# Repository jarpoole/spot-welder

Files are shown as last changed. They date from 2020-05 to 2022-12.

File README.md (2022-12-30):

# Spot Welder

## Features

1. Precise microsecond timing resolution selected via an encoder wheel.
2. Three user-programmable timing presets which are accessible via the buttons.
3. A 1/4 inch jack for an external footpedal. See the `mechanical` folder for a simple 3D printable footpedal design.

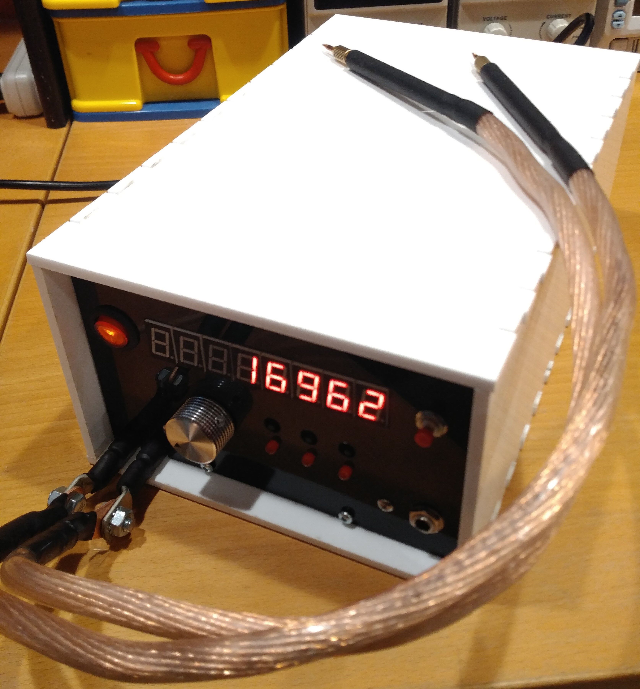
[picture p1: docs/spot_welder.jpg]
Spot Welder


## Internals

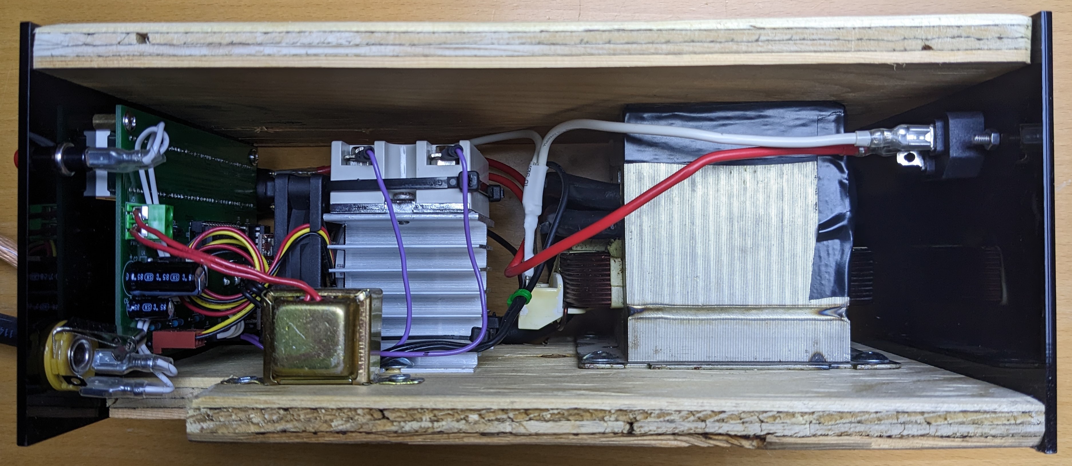
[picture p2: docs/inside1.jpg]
inside1


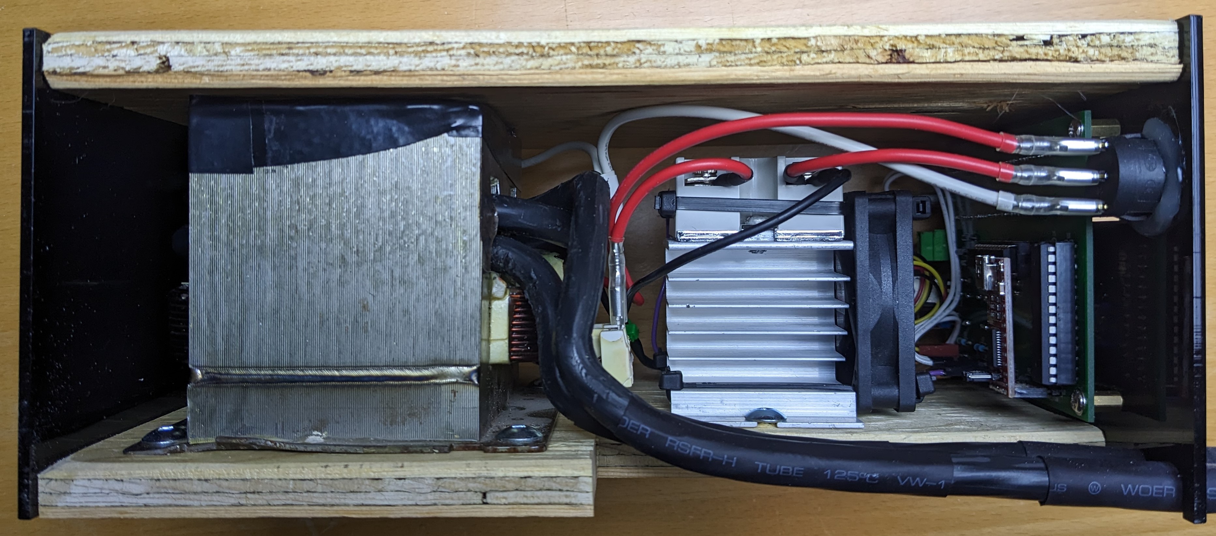
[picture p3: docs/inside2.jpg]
inside2


## Principles of Operation

The spot welder is build around a recycled microwave transformer which has had its secondary coil rewound to produce a high current and low voltage (2 turns of 4AWG). The microwave and unmodified transformer are shown below.

microwave

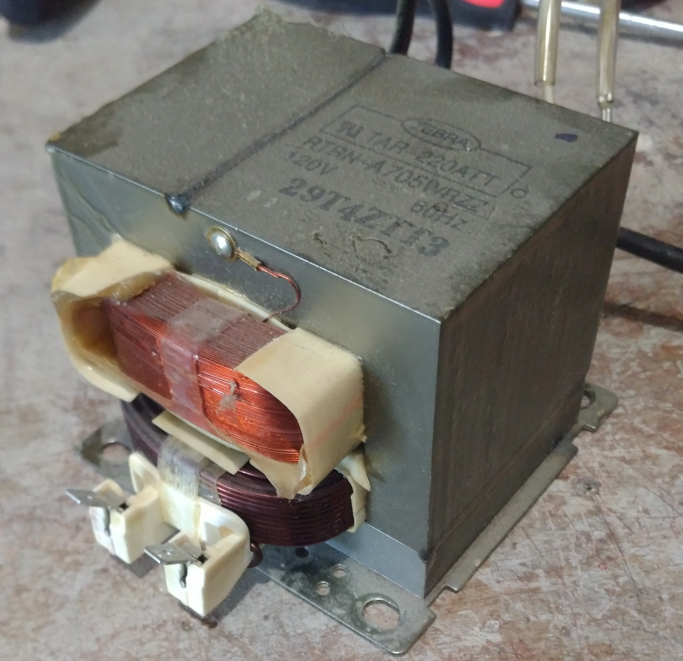
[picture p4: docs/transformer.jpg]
transformer


 A solid state relay (SSR) is used to create precise pulses to produce welds by controlling the primary side. Because of the large currents that it will need to handle it is heatsunk and actively cooled with a small computer fan.

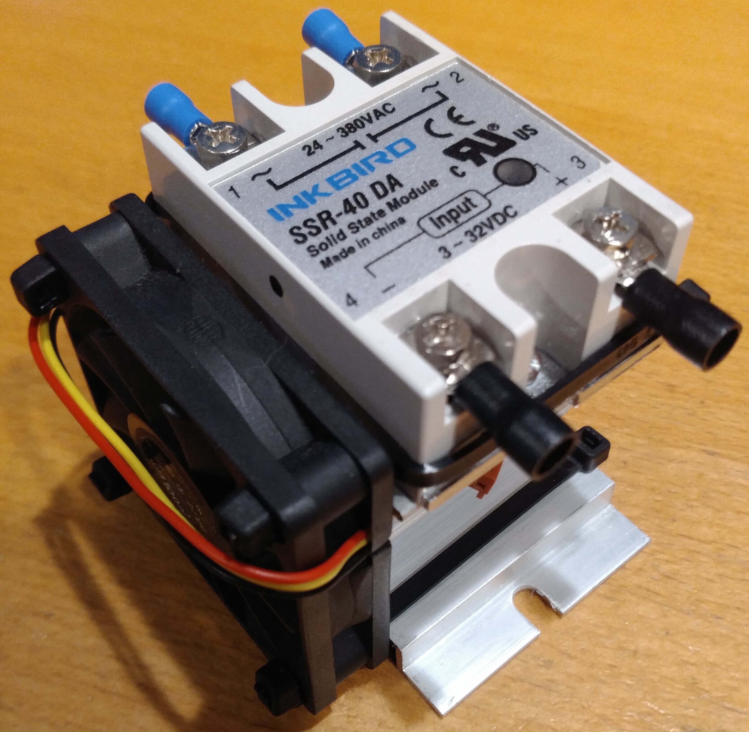
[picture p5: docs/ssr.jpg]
ssr


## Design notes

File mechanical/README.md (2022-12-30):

# Mechanical

## Footswitch

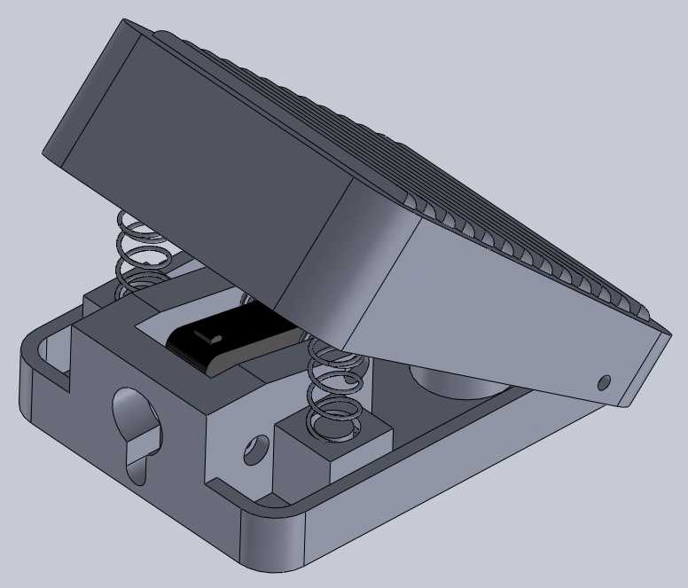
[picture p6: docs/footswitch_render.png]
footswitch


## Enclosure

The [front plate](./enclosure/front_plate.pdf) and [back plate](./enclosure/back_plate.pdf) are each around `185x130mm` and should be cut out of `3mm` acrylic.

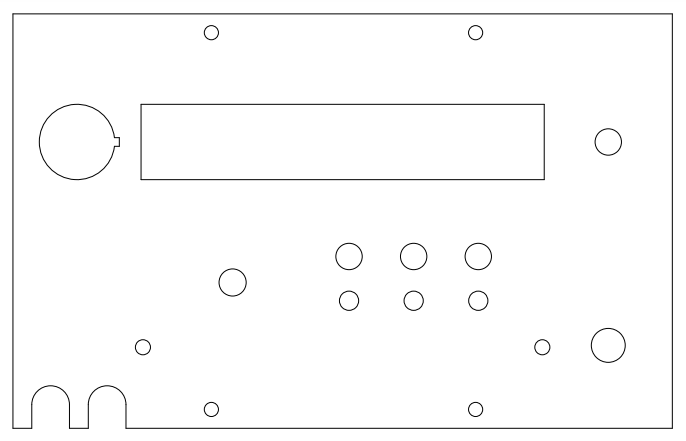
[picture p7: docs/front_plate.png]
front plate

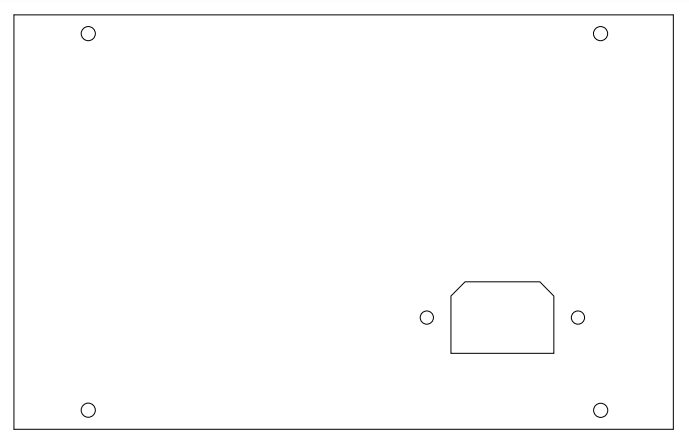
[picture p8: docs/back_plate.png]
back plate


The [shell](./enclosure/shell.pdf) requires an entire `18x24inch` sheet of 6mm acrylic.

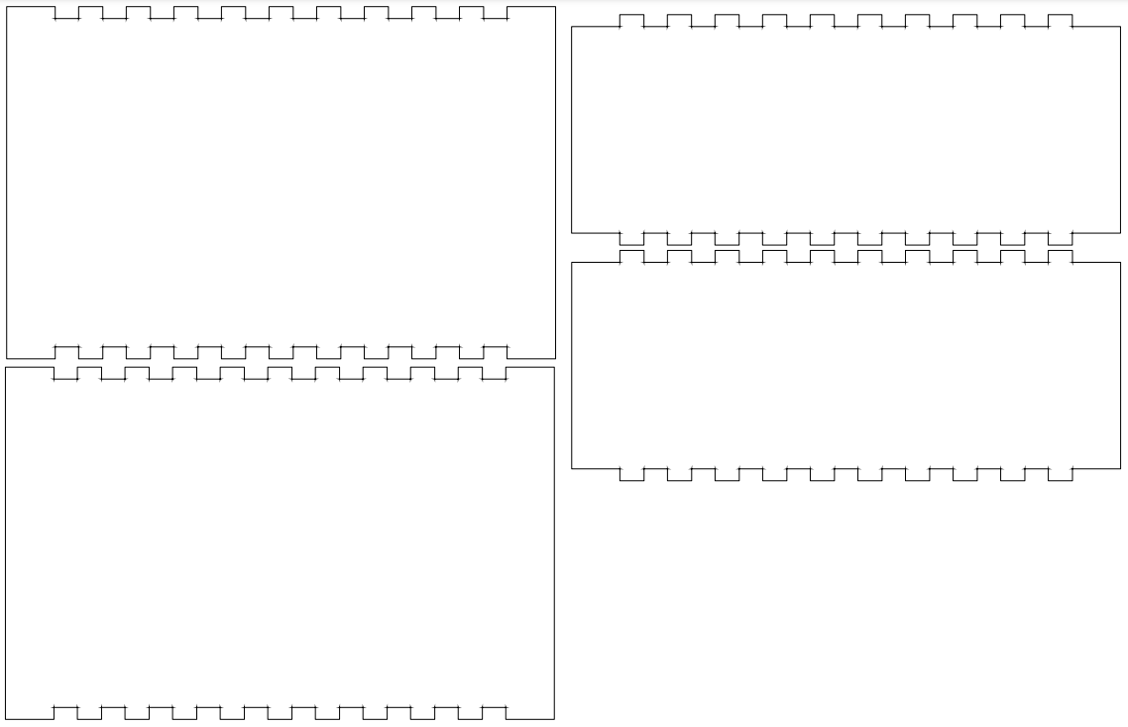
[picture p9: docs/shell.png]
shell


Finally, some small external buttons are required to extend the tactile switches on the PCB. The CAD file `button.step` is provided and can be easily 3D printed.

## Other

3 small 8mm button extenders are also needed. Their CAD model is `button.stl`.

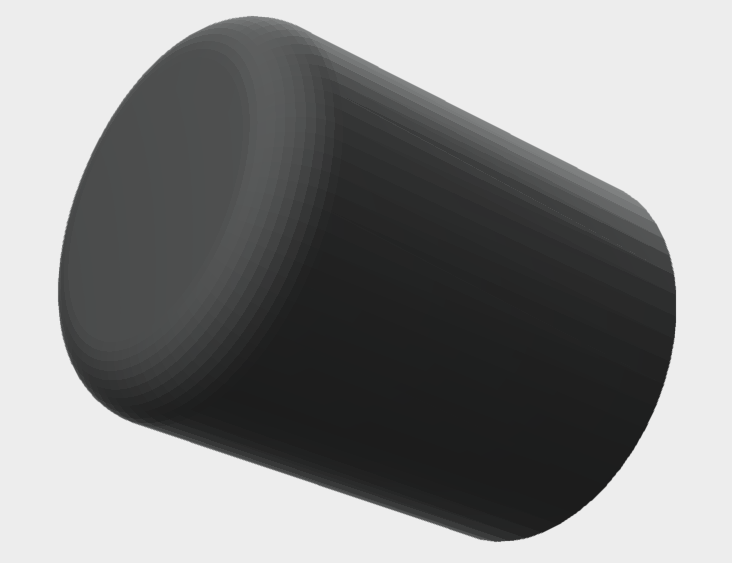
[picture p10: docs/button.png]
button


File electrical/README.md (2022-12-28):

# Electrical

## Design Software

Designed with [DipTrace](https://diptrace.com/). Sourcefiles for both the schematic (`schematic.dch`) and pcb (`pcb.dip`) are provided.

## Schematic

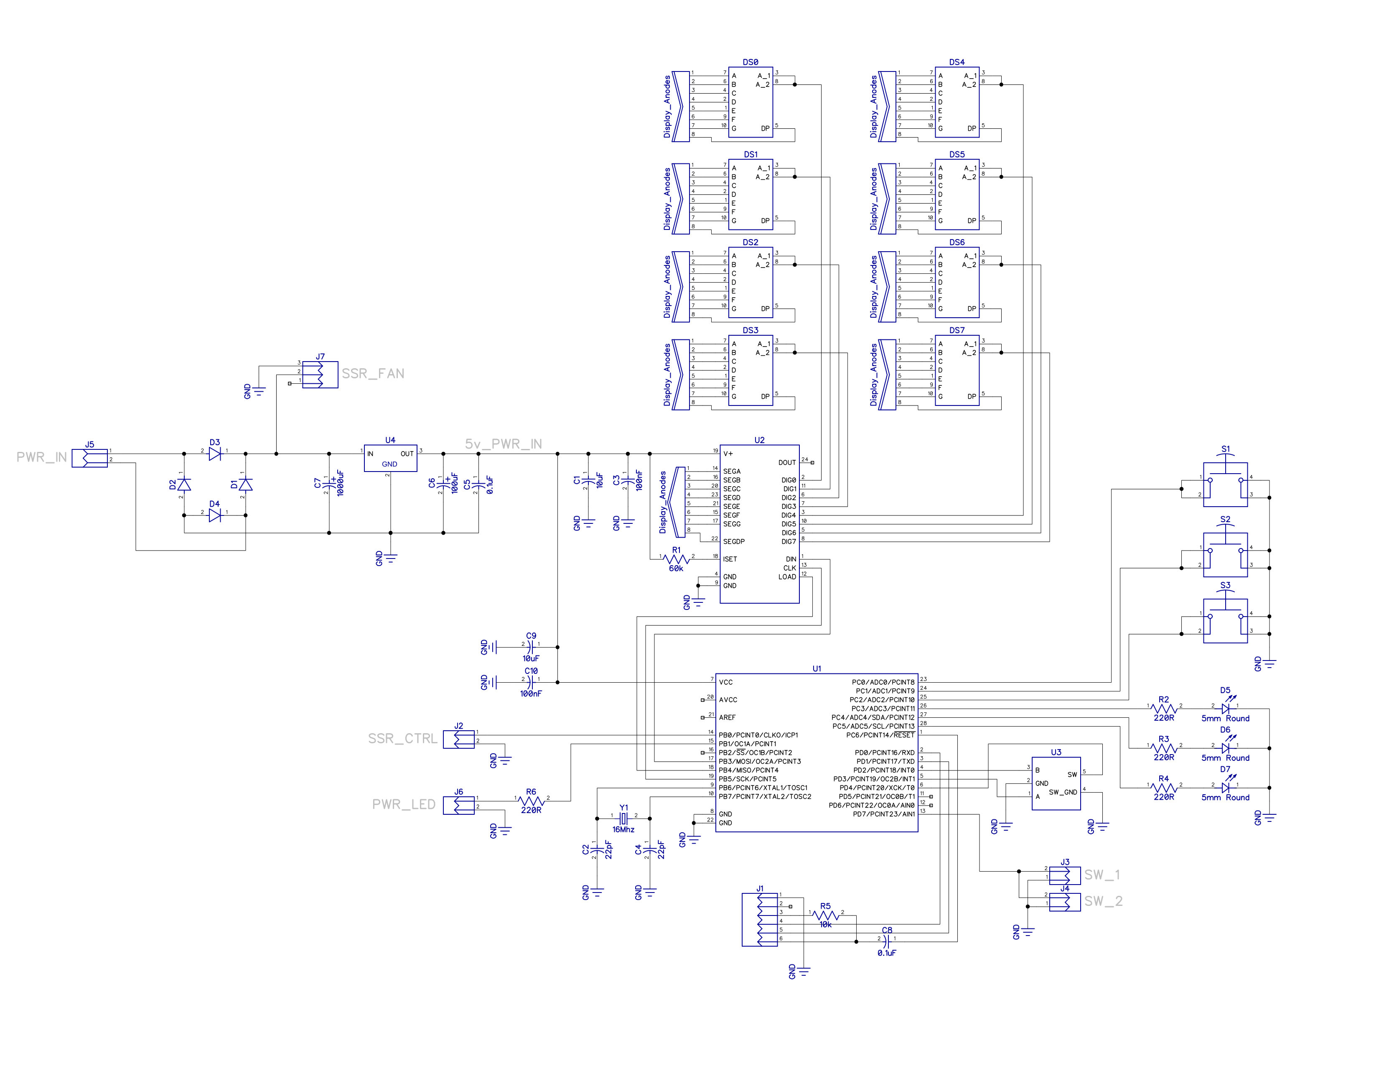
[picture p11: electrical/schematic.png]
schematic


## PCB

Most of the 3D models used for these renders are included in DipTrace's 3D model [download](https://diptrace.com/download/libraries-and-3d-models/). The models for the encoder and one of the terminal blocks are included in the `3rd_party` directory.

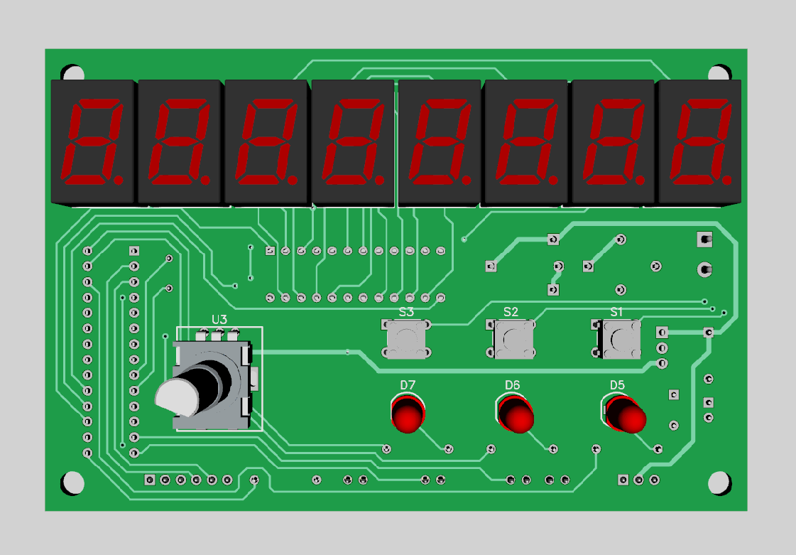
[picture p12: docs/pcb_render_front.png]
front

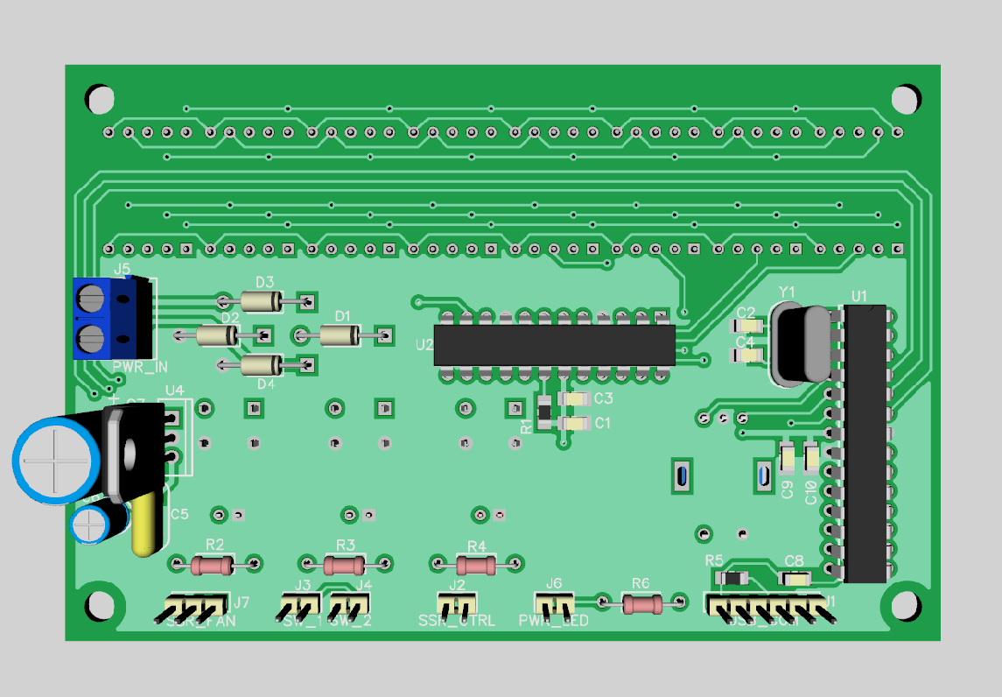
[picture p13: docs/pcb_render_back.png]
back


The generated mechanical model is also provided as `pcb.step`.

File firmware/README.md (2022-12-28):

# Firmware

## Dependencies

This project depends on the excellent `MAX7219` driver by `wayoda`. See their repository for installation instructions.

https://github.com/wayoda/LedControl
https://reference.arduino.cc/reference/en/libraries/ledcontrol/

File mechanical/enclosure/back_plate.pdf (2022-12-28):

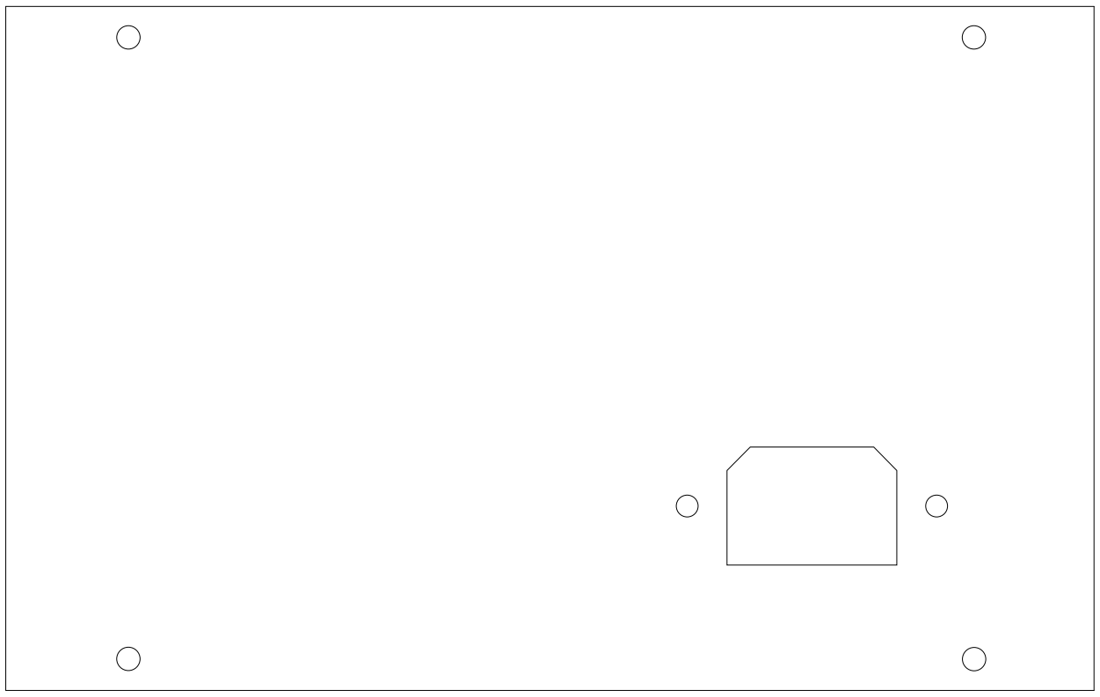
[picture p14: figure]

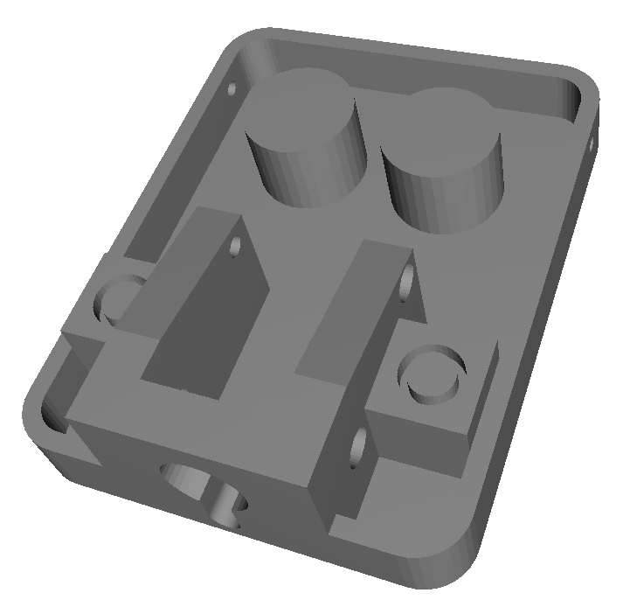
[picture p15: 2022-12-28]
docs/footswitch_base.png

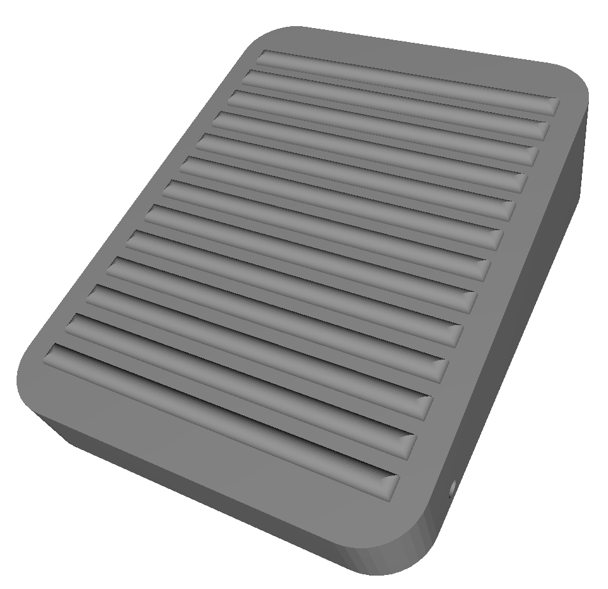
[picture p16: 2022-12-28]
docs/footswitch_top.png

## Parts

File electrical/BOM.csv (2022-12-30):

Name | Manufacturer | Quantity | RefDes | Value
CAP_1206 |  | 2 | C1, C9 | 10uF
CAP_1206 |  | 2 | C2, C4 | 22pF
CAP_1206 |  | 2 | C3, C10 | 100nF
CAP200 |  | 1 | C5 | 0.1uF
CAP100RP |  | 1 | C6 | 100uF
CAP300RP |  | 1 | C7 | 1000uF
CAP_1206 |  | 1 | C8 | 0.1uF
1N4001 |  | 4 | D1, D2, D3, D4
LED-5R_Red | Kingbright | 3 | D5, D6, D7 | 5mm Round
SA56-11EWA |  | 8 | DS0, DS1, DS2, DS3, DS4, DS5, DS6, DS7
644456-6 | TE Connectivity | 1 | J1
2 pin 2.54mm Term Block |  | 4 | J2, J3, J4, J6
OSTTA020161B | On Shore Technology | 1 | J5
644456-3 | TE Connectivity | 1 | J7
RES_1206 |  | 1 | R1 | 60k
RES400 |  | 4 | R2, R3, R4, R6 | 220R
RES_1206 |  | 1 | R5 | 10k
B3F-1000 | OMRON | 3 | S1, S2, S3
ATMEGA328_PDIP28 | Atmel | 1 | U1
MAX7219CNG | Maxim | 1 | U2
Rotary Encoder |  | 1 | U3
LM7805CT | National Semiconductor | 1 | U4
HC49S |  | 1 | Y1 | 16Mhz

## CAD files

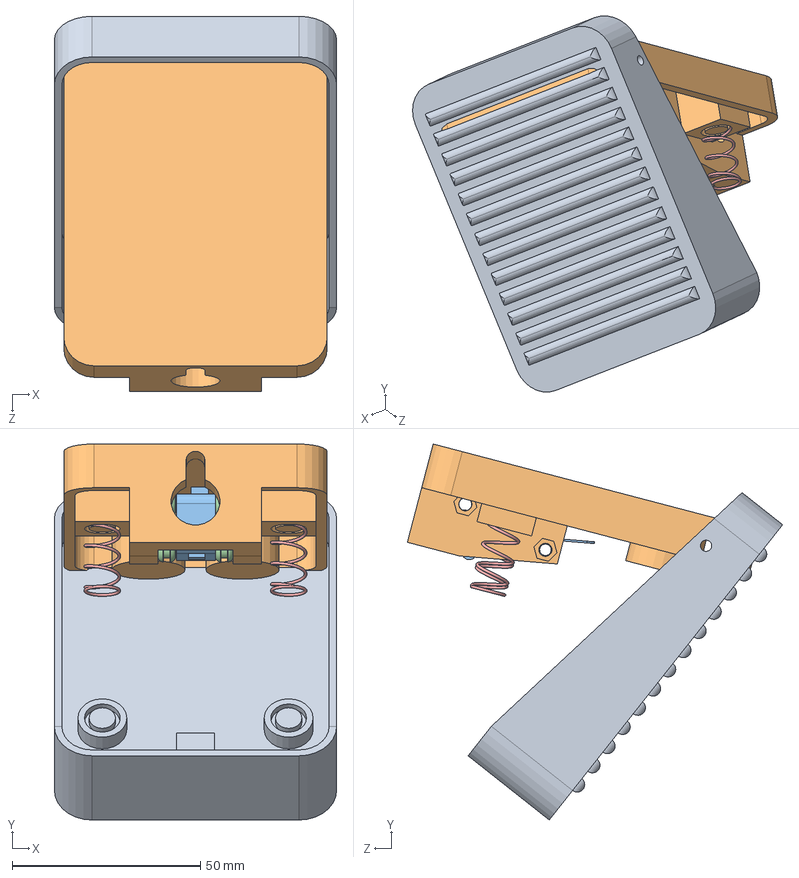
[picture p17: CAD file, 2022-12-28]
mechanical/footswitch/footswitch.SLDASM
75.0 x 99.9 x 99.7 mm
pedal
Pedal Base
V_153_1C25_BASE
Bushing x 4
Spring x 2

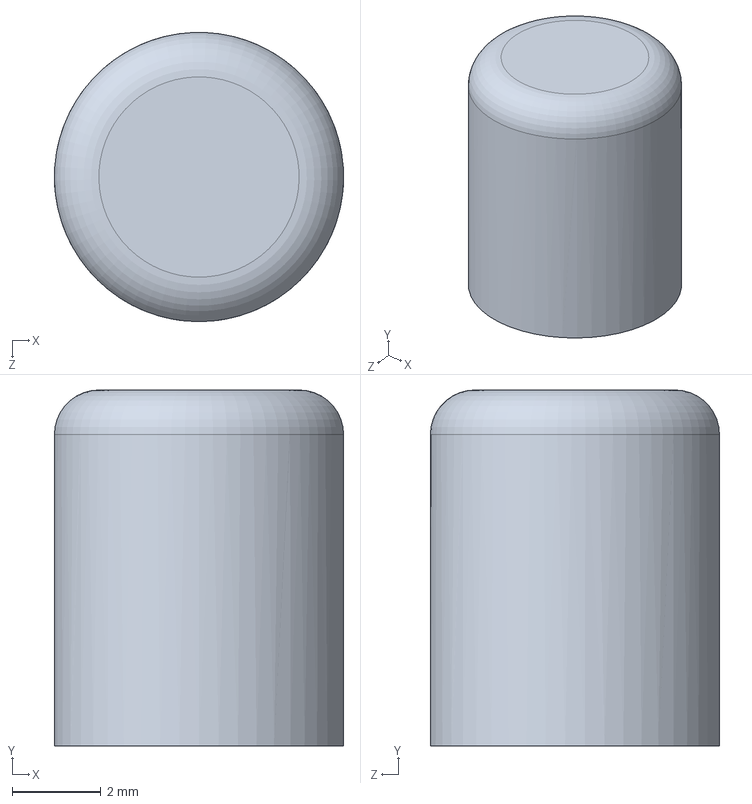
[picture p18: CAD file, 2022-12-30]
mechanical/button.SLDPRT
6.50 x 8.00 x 6.50 mm

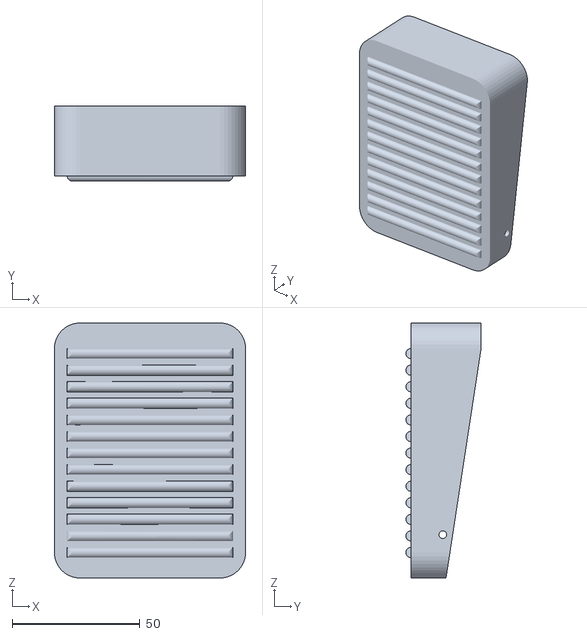
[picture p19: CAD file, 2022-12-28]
mechanical/footswitch/top.STL
75.0 x 29.5 x 100.0

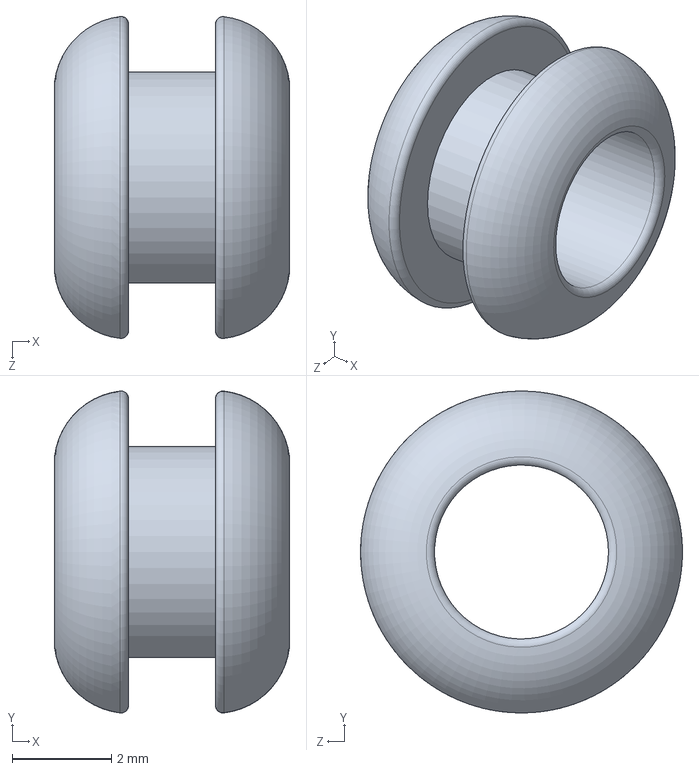
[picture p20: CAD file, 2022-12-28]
mechanical/footswitch/bushing.SLDPRT
4.73 x 6.48 x 6.48 mm

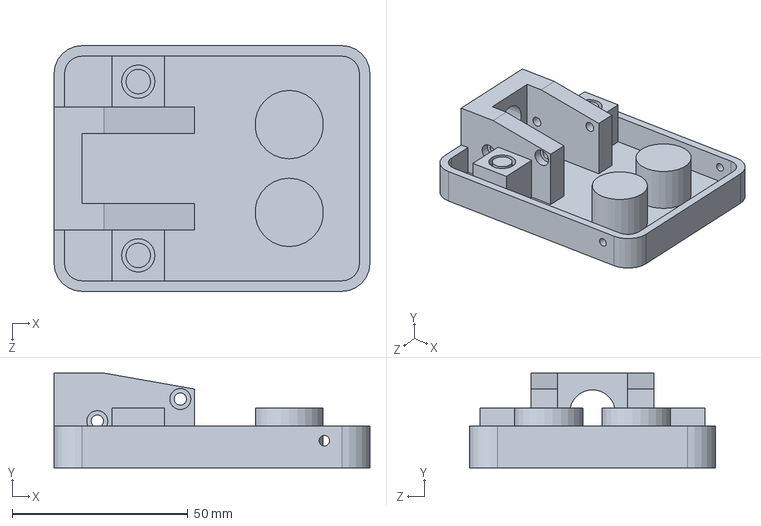
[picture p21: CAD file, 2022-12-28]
mechanical/footswitch/base.SLDPRT
90.0 x 27.0 x 70.0 mm

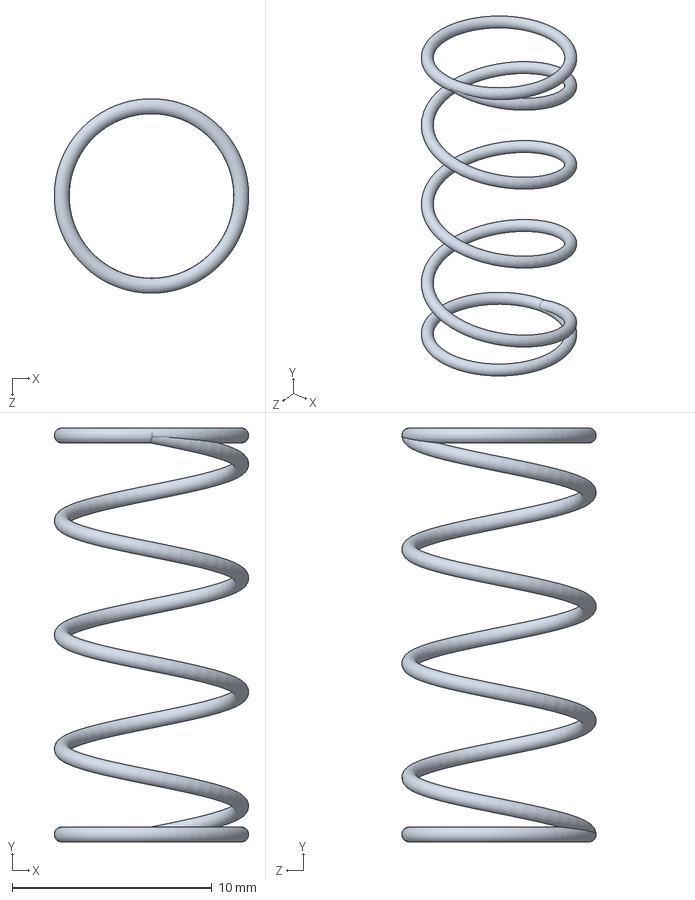
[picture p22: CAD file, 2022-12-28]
mechanical/footswitch/spring.SLDPRT
9.75 x 20.8 x 9.75 mm

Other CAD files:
mechanical/footswitch/pedal.SLDPRT
mechanical/button.STL
mechanical/footswitch/base.STL

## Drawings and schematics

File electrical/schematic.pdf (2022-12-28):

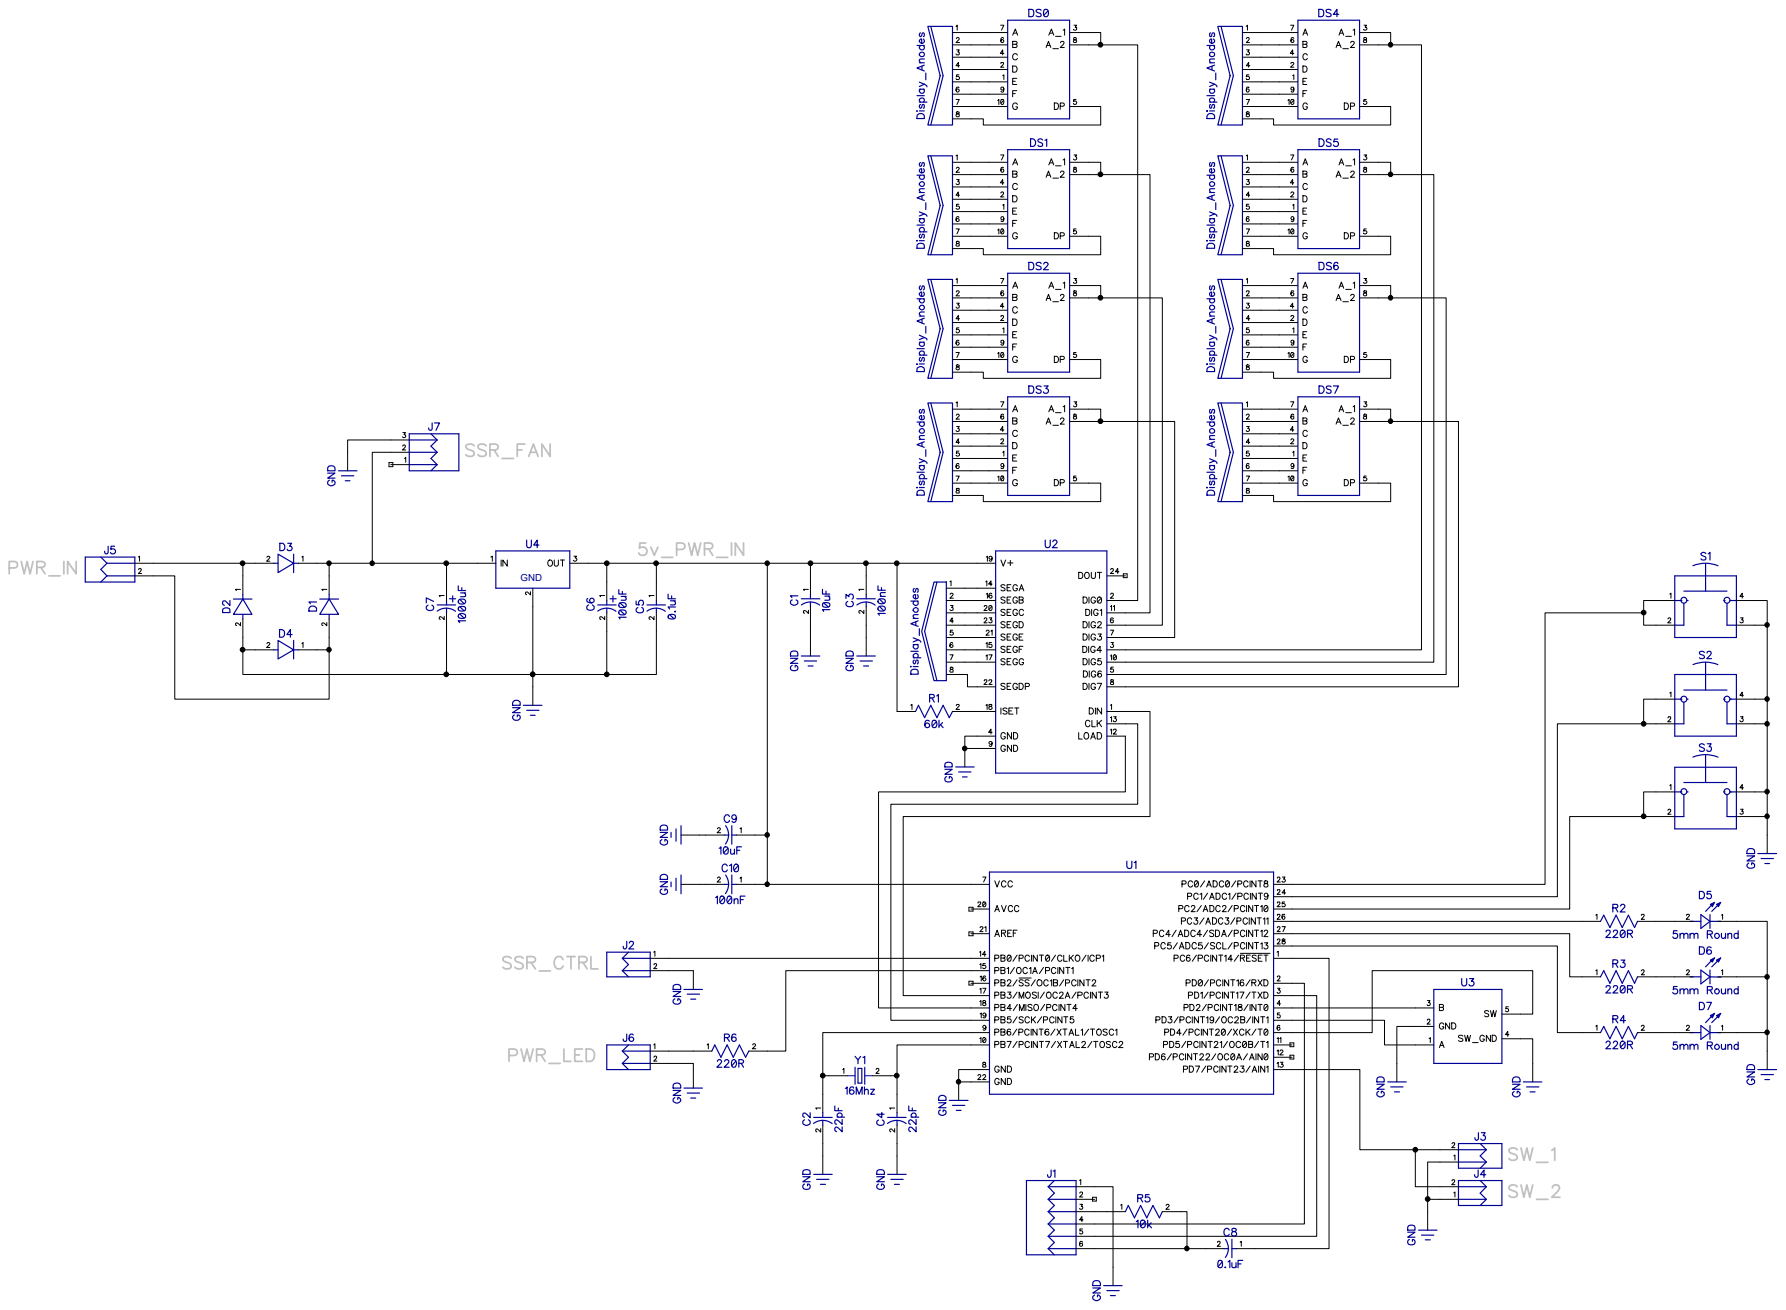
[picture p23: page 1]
GND

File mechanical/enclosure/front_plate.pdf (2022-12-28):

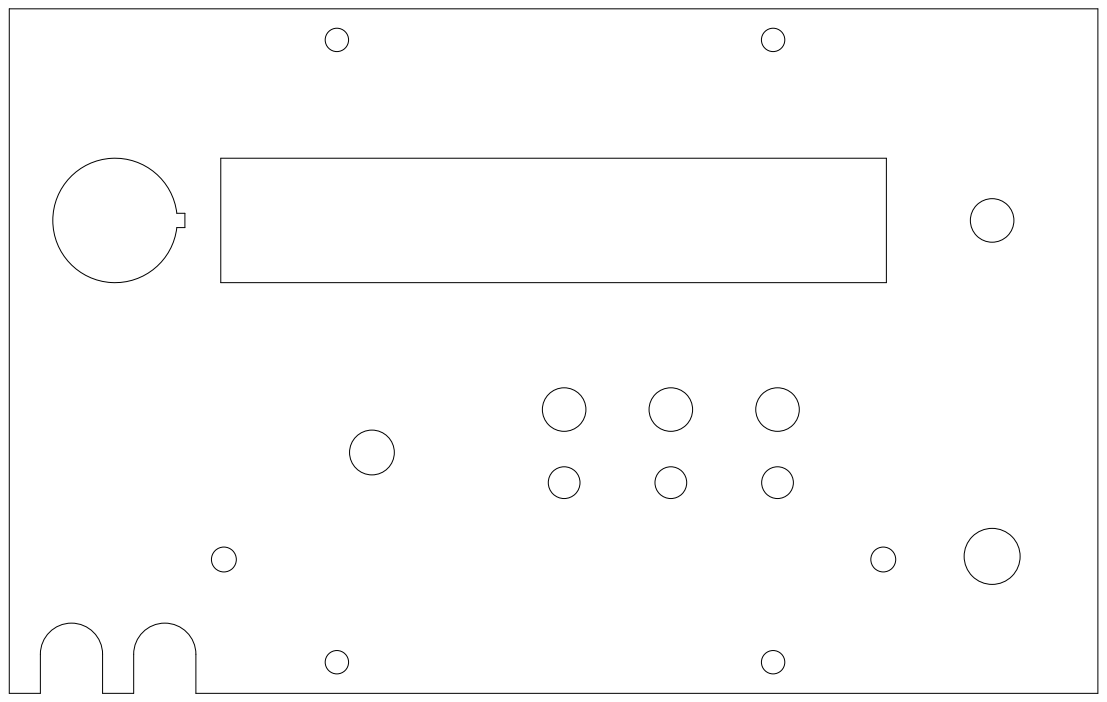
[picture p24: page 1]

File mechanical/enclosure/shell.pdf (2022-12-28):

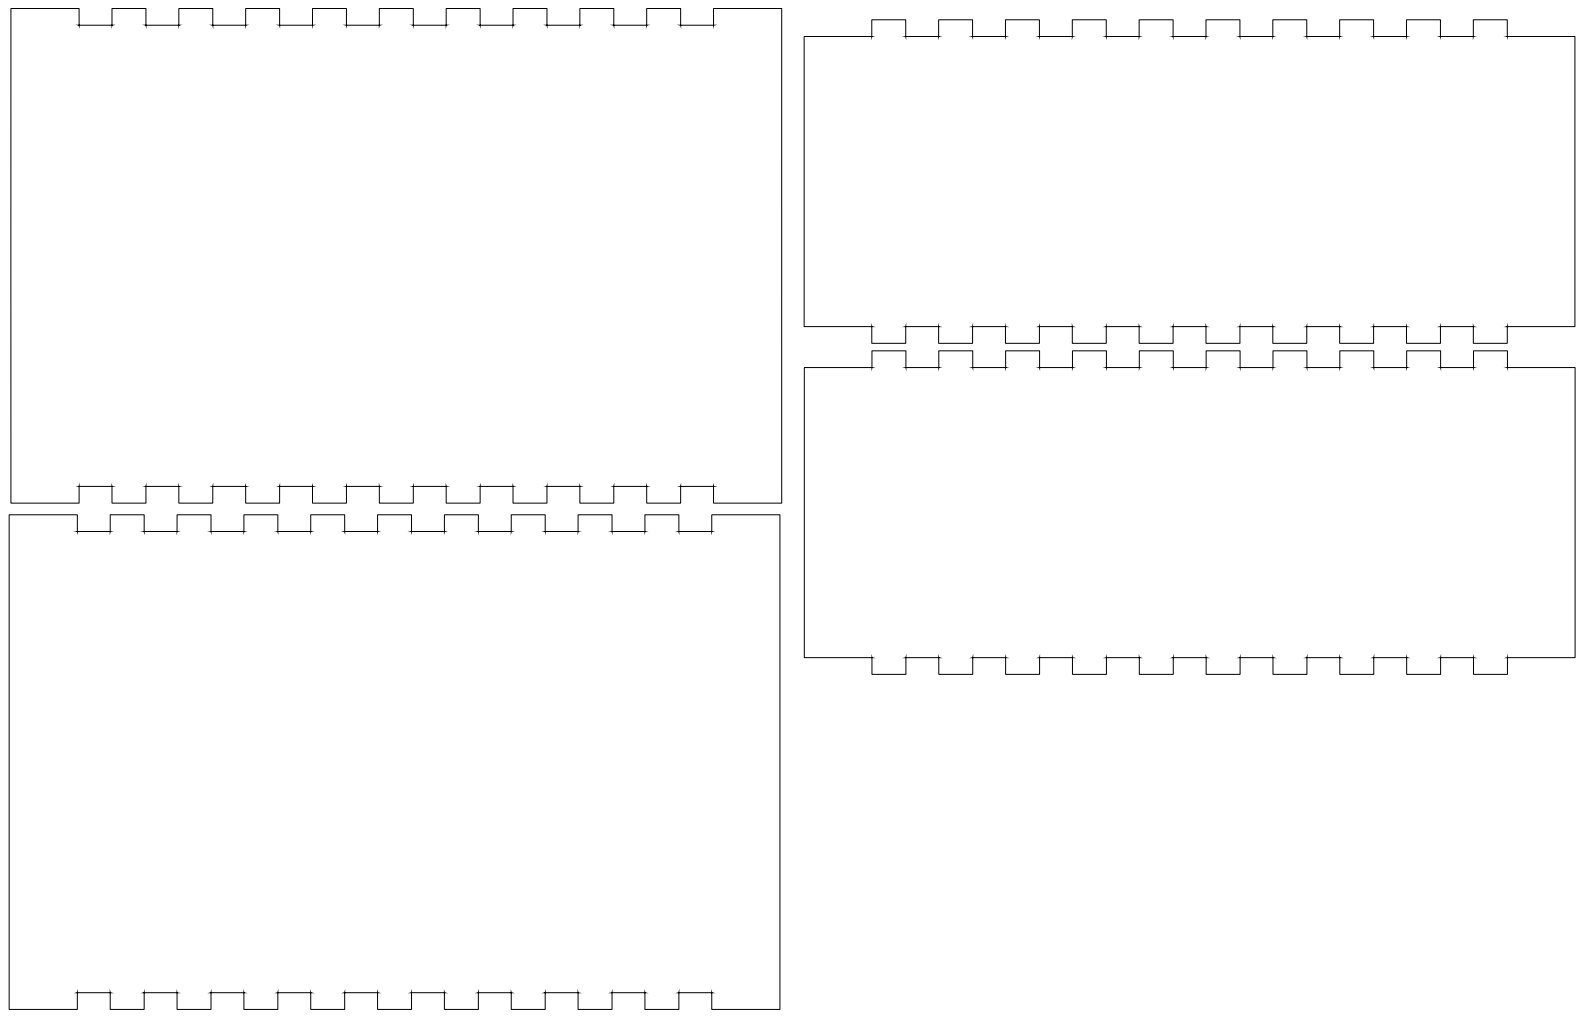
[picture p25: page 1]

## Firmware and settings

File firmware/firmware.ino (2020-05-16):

#include "LedControl.h"
#include <EEPROM.h>

// DataIn=11, CLK=13, LOAD=12, #MAX7219 devices
LedControl lc=LedControl(11,13,12,1);
//Wait a bit between updates of the display
unsigned long delaytime=250;

//Encoder Stuff
static int pinA = 2; // Our first hardware interrupt pin is digital pin 2
static int pinB = 3; // Our second hardware interrupt pin is digital pin 3
static int encoderButton = 4; // Encoder button pin
volatile byte aFlag = 0; // let's us know when we're expecting a rising edge on pinA to signal that the encoder has arrived at a detent
volatile byte bFlag = 0; // let's us know when we're expecting a rising edge on pinB to signal that the encoder has arrived at a detent (opposite direction to when aFlag is set)
volatile byte reading = 0; //somewhere to store the direct values we read from our interrupt pins before checking to see if we have moved a whole detent
volatile bool lastButtonState = false; //Last value of the encoder button
volatile long lastTickTime = 0; //Used to calculate encoder acceleration

//Control data
static int button1 = A2;
static int button2 = A1;
static int button3 = A0;
static int led1 = A5;
static int led2 = A4;
static int led3 = A3;
static long button1Time = 0;
static long button2Time = 0;
static long button3Time = 0;
static int longPressTime = 2000;
static int triggerPin = 7;
static int ssrPin = 8;
static int buzzerPin = 9;

static int blinkTime = 200;
volatile long blinkTimer = 0;
volatile bool blinking = false;

volatile uint32_t incrementValue = 1;
volatile uint32_t incrementPos = 0;

static int eepromPreset1Start = 5; //Each uint32_t occupies 4 bytes
static int eepromPreset2Start = 9;
static int eepromPreset3Start = 13;
volatile uint32_t preset1 = 0;
volatile uint32_t preset2 = 0;
volatile uint32_t preset3 = 0;

volatile uint32_t weldTime = 0;
volatile long lastWeldTime = 0; //Time in millis that the last weld occured at
static int weldTimeout = 3000;  //Minimum time before next weld

volatile bool refresh = false;


void setup() {
  pinMode(pinA, INPUT_PULLUP); // set pinA as an input, pulled HIGH to the logic voltage (5V or 3.3V for most cases)
  pinMode(pinB, INPUT_PULLUP); // set pinB as an input, pulled HIGH to the logic voltage (5V or 3.3V for most cases)
  attachInterrupt(0,PinA,RISING); // set an interrupt on PinA, looking for a rising edge signal and executing the "PinA" Interrupt Service Routine (below)
  attachInterrupt(1,PinB,RISING); // set an interrupt on PinB, looking for a rising edge signal and executing the "PinB" Interrupt Service Routine (below)
  Serial.begin(9600); // start the serial monitor link

  pinMode(encoderButton, INPUT_PULLUP);
  pinMode(button1, INPUT_PULLUP);
  pinMode(button2, INPUT_PULLUP);
  pinMode(button3, INPUT_PULLUP);
  pinMode(triggerPin, INPUT_PULLUP);

  pinMode(led1, OUTPUT);
  pinMode(led2, OUTPUT);
  pinMode(led3, OUTPUT);
  pinMode(buzzerPin, OUTPUT);
  pinMode(ssrPin, OUTPUT);

  preset1 = recallPreset(eepromPreset1Start);
  preset2 = recallPreset(eepromPreset2Start);
  preset3 = recallPreset(eepromPreset3Start);

  Serial.println(preset1);
  Serial.println(preset2);
  Serial.println(preset3);
  
  // The MAX7219 is in power-saving mode on startup, we have to do a wakeup call
  lc.shutdown(0,false);
  // Set the brightness (0-15) to full
  lc.setIntensity(0,15);
  // Clear the display
  lc.clearDisplay(0);
}

void loop() {

  if( !digitalRead(triggerPin) && millis() > (lastWeldTime + weldTimeout) ){
    //Timer setup
    int milliseconds = weldTime / 1000;
    int microseconds = weldTime % 1000;

    Serial.println(weldTime);
    
    digitalWrite(buzzerPin, HIGH);
    digitalWrite(ssrPin, HIGH);

    if(milliseconds){
      delay(milliseconds);
    }
    if(microseconds){
      delayMicroseconds(microseconds);
    }
    
    digitalWrite(ssrPin, LOW);
    digitalWrite(buzzerPin, LOW);
    lastWeldTime = millis();
  }

  //Timer for blinking decimal point selection indicator
  if(millis() > blinkTimer){
    blinkTimer = millis() + blinkTime;
    blinking = !blinking;
    refresh = true;
  }

  if(!digitalRead(encoderButton)){
    if(incrementValue > 1000000 || incrementValue == 0){
      incrementValue = 1;
      incrementPos = 0;
    }else{
      incrementValue = incrementValue * 10;
      incrementPos++;
    }
    refresh = true;
    delay(250);
  }

  if(!digitalRead(button1) && button1Time == 0){
    button1Time = millis();
    refresh = true;
  }
  if(!digitalRead(button2) && button2Time == 0){
    button2Time = millis();
    refresh = true;
  }
  if(!digitalRead(button3) && button3Time == 0){
    button3Time = millis();
    refresh = true;
  }

  if( digitalRead(button1) ){
    if( button1Time == 0){
      //Do nothing
    }else if(millis() - button1Time > longPressTime){ //save
      button1Time = 0;
      savePreset(eepromPreset1Start, weldTime);
      preset1 = weldTime;
      for(int i = 0; i < 3; i++){
        digitalWrite(led1, HIGH);
        delay(blinkTime);
        digitalWrite(led1, LOW);
        delay(blinkTime);
      }
      refresh = true;
    }else{  //recall
      weldTime = preset1;
      button1Time = 0;
      digitalWrite(led1, HIGH);
      digitalWrite(led2, LOW);
      digitalWrite(led3, LOW);
      refresh = true;
    }
  }

  if( digitalRead(button2) ){
    if( button2Time == 0){
      //Do nothing
    }else if(millis() - button2Time > longPressTime){ //save
      button2Time = 0;
      savePreset(eepromPreset2Start, weldTime);
      preset2 = weldTime;
      for(int i = 0; i < 3; i++){
        digitalWrite(led2, HIGH);
        delay(blinkTime);
        digitalWrite(led2, LOW);
        delay(blinkTime);
      }
      refresh = true;
    }else{  //recall
      weldTime = preset2;
      button2Time = 0;
      digitalWrite(led1, LOW);
      digitalWrite(led2, HIGH);
      digitalWrite(led3, LOW);
      refresh = true;
    }
  }

  if( digitalRead(button3) ){
    if( button3Time == 0){
      //Do nothing
    }else if(millis() - button3Time > longPressTime){ //save
      button3Time = 0;
      savePreset(eepromPreset3Start, weldTime);
      preset3 = weldTime;
      for(int i = 0; i < 3; i++){
        digitalWrite(led3, HIGH);
        delay(blinkTime);
        digitalWrite(led3, LOW);
        delay(blinkTime);
      }
      refresh = true;
    }else{  //recall
       weldTime = preset3;
       button3Time = 0;
       digitalWrite(led1, LOW);
       digitalWrite(led2, LOW);
       digitalWrite(led3, HIGH);
       refresh = true;
    }
  }

  if(refresh) {
    //Serial.println(weldTime);
    updateDisplay(weldTime, blinking, incrementPos);
    refresh = false;
  }
  
  
  //delay(delaytime);

}

void PinA(){
  cli(); //stop interrupts happening before we read pin values
  reading = PIND & 0xC; // read all eight pin values then strip away all but pinA and pinB's values
  if(reading == B00001100 && aFlag) { //check that we have both pins at detent (HIGH) and that we are expecting detent on this pin's rising edge
    weldTime += incrementValue; //increment the encoder's position count
    bFlag = 0; //reset flags for the next turn
    aFlag = 0; //reset flags for the next turn
    digitalWrite(led1, LOW);
    digitalWrite(led2, LOW);
    digitalWrite(led3, LOW);
  }
  else if (reading == B00000100) bFlag = 1; //signal that we're expecting pinB to signal the transition to detent from free rotation
  refresh = true;
  sei(); //restart interrupts
}
void PinB(){
  cli(); //stop interrupts happening before we read pin values
  reading = PIND & 0xC; //read all eight pin values then strip away all but pinA and pinB's values
  if (reading == B00001100 && bFlag) { //check that we have both pins at detent (HIGH) and that we are expecting detent on this pin's rising edge

    if(weldTime - incrementValue < weldTime){ //Detect integer underflow
      weldTime = weldTime - incrementValue;  //decrement the encoder's position count
    }else{
      weldTime = 0;
    }
    
    bFlag = 0; //reset flags for the next turn
    aFlag = 0; //reset flags for the next turn
    digitalWrite(led1, LOW);
    digitalWrite(led2, LOW);
    digitalWrite(led3, LOW);
  }
  else if (reading == B00001000) aFlag = 1; //signal that we're expecting pinA to signal the transition to detent from free rotation
  refresh = true;
  sei(); //restart interrupts
}

//Device#, digit#, value, decimal
//lc.setDigit(0,0,5,false)
void updateDisplay(uint32_t value, bool blinking, int blinkingPos){
  lc.clearDisplay(0);
  if(value == 0){
    lc.setDigit(0, 0, 0, false);
  }else{
    int c = 0; 
    while (value != 0){
      lc.setDigit(0, c, value % 10, false);
      value /= 10;
      c++;
    }
  }

  //Device#, row#, col#, decimal
  lc.setLed(0, blinkingPos, 0, blinking);
}

void savePreset(int presetStartAddr, uint32_t value){
  byte upper = value >> 24;
  byte upMid = (value << 8) >> 24;
  byte lowMid = (value << 16) >> 24;
  byte lower = (value << 24) >> 24;
  
  EEPROM.write(presetStartAddr, upper);
  EEPROM.write(presetStartAddr + 1, upMid);
  EEPROM.write(presetStartAddr + 2, lowMid);
  EEPROM.write(presetStartAddr + 3, lower);
  
  Serial.print("Saved value: ");
  Serial.print(value);
  Serial.print("\n");
}

uint32_t recallPreset(int presetStartAddr){
  byte upper = EEPROM.read(presetStartAddr);
  byte upMid = EEPROM.read(presetStartAddr + 1);
  byte lowMid = EEPROM.read(presetStartAddr + 2);
  byte lower = EEPROM.read(presetStartAddr + 3);

  uint32_t value = ((uint32_t) upper << 24) | ((uint32_t) upMid << 16) | ((uint32_t) lowMid << 8) | ((uint32_t) lower);

  Serial.print("Read value: ");
  Serial.print(value);
  Serial.print("\n");
  
  return value;
}

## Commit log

2020-05-16 Fixed EEPROM storage method
    [firmware.ino]
2022-12-28 Added electrical + mechanical
    [BOM.csv]
2022-12-28 Added more docs (#3)
    [base.SLDPRT, base.STL, bushing.SLDPRT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]
2022-12-30 Docs (#4)
    [button.SLDPRT]
